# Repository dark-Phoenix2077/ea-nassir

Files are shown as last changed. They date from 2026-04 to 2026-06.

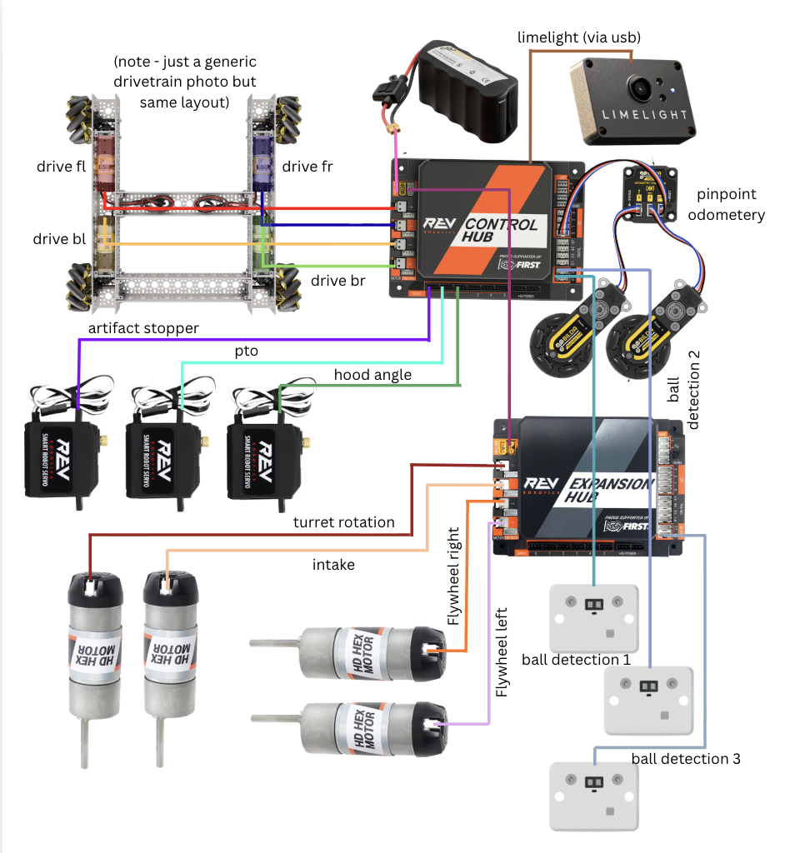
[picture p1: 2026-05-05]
wiring.png

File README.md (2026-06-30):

## ea-nassir 
A robot made to compete in the FTC decode season, built just to practise cad and coding skills =)

Screenshot 2026-04-23 at 11 40 23 am

## build photos





## why I made this

I wanted to attempt making a full FTC robot from scrach, on my own. despite my final design turning out very similar to widespread designs, I am happy just for building one of my own from scratch. I probably will not take part in any competitions, but I have been wanting to go through the whole process of building an FTC robot from start to finish, and the stasis hackathon finally gave me an excuse to do so.

## what there is

Currently, I have done the following:

CAD: The most complete, comprehensive part of the design, this consists of silicon molds for custom intake rollers, a drivetrain, 360 turret and PTO mechanism, all connected with custom CNC plates.

Screenshot 2026-04-23 at 12 18 12 pm

Screenshot 2026-04-23 at 12 18 51 pm

Screenshot 2026-04-23 at 12 19 32 pm

Screenshot 2026-04-23 at 12 31 41 pm

Coding: all set up and completed except for specific pedropathing parameters, will do when I build the physical robot (needs specific calibration)

Screenshot 2026-04-23 at 12 33 21 pm

(note that code is in /TeamCode/src/main/java/org/firstinspires/ftc/teamcode)

BOM: created a (as comprehensive as I could remember) BOM

Wiring: also added the wiring diagram for all motors/servos/sensors/etc. - in WIRING.md

## BOM

(note that this may not be final. also, most of these parts already exist with me)

Electronics & Control

| # | Name | Item Code | Qty | Notes | Link |
|---|---|---|-----|---|---|
| 1 | REV Control Hub | REV-31-1595 | 1 | Main robot controller | [Link](https://www.revrobotics.com/rev-31-1595/) |
| 2 | REV Expansion Hub | REV-31-1153 | 1 | Adds extra I/O ports | [Link](https://www.revrobotics.com/rev-31-1153/) |
| 3 | Axon MAX Servo | — | 2 | High-torque smart servo | [Link](https://axon-robotics.com/products/max) |
| 4 | GoBilda 5000 Series 12VDC Motor | 5000-0002-0001 | 2 | 12V DC motor, no encoder | [Link](https://www.gobilda.com/5000-series-12vdc-motor/) |
| 5 | GoBilda 5000 Series 12VDC Motor (REX Pinion Shaft) | 5000-0002-4008 | 1 | 12V DC motor with 8mm REX pinion shaft | [Link](https://www.gobilda.com/5000-series-12vdc-motor-with-8mm-rex-pinion-shaft/) |
| 6 | 5203 Series Yellow Jacket Planetary Gear Motor (13.7:1) | 5203-2402-0014 | 4 | 435 RPM, 8mm REX shaft, 3.3–5V encoder | [Link](https://www.gobilda.com/5203-series-yellow-jacket-planetary-gear-motor-13-7-1-ratio-24mm-length-8mm-rex-shaft-435-rpm-3-3-5v-encoder/) |
| 7 | 5203 Series Yellow Jacket Planetary Gear Motor (1:1) | 5203-242-0001 | 1 | 6000 RPM, 8mm REX shaft, 3.3–5V encoder | [Link](https://www.gobilda.com/5203-series-yellow-jacket-motor-1-1-ratio-24mm-length-8mm-rex-shaft-6000-rpm-3-3-5v-encoder/) |
| 8 | REV Through Bore Encoder | REV-11-3174 | 1 | Magnetic rotary encoder | [Link](https://www.revrobotics.com/rev-11-3174) |
| 9 | 6V Servo Power Injector (6 Channel, 8–15V Input) | 3125-0001-0001 | 1 | Powers servos independently from hubs | [Link](https://www.gobilda.com/6v-servo-power-injector-6-channel-8-15v-input/) |

 Sensors

| # | Name | Item Code | Qty | Notes | Link |
|---|---|---|-----|---|---|
| 10 | Swyft Ranger Distance Sensor | — | 3 | Distance sensor | [Link](https://swyftrobotics.com/products/swyft-ranger-distance-sensor) |
| 11 | REV Magnetic Limit Switch Bundle | REV-31-1462 | 1 | Bundle includes REV-40-1467 switch | [Link](https://www.revrobotics.com/rev-31-1462/) |
| 12 | REV Magnet Limit Switch (individual) | REV-40-1467 (inside REV-31-1462) | 1 | Part of the bundle above | [Link](https://www.revrobotics.com/rev-31-1462/) |

Odometry & Navigation

| # | Name | Item Code | Qty | Notes | Link |
|---|---|---|-----|---|---|
| 13 | GoBilda Pinpoint Odometry Pod (32mm wheel) | 3110-0001-0002 | 3 | 2 for drivetrain, 1 for other use | [Link](https://www.gobilda.com/4-bar-odometry-pod-32mm-wheel/) |

Drivetrain

| # | Name | Item Code | Qty | Notes | Link |
|---|---|---|-----|---|---|
| 14 | Mecanum Wheel Set 96mm (70A, Bearing Supported) | 3213-3606-0002 | 4 (1 pack of 4) | Main drivetrain wheels | [Link](https://www.gobilda.com/96mm-mecanum-wheel-set-70a-durometer-bearing-supported-rollers/) |
| 15 | 3417 Series 5mm HTD Pinion Timing Belt Pulley (8mm REX, 16T) | 3417-4008-0016 | 4 | Drivetrain belt drive | [Link](https://www.gobilda.com/3417-series-5mm-htd-pitch-set-screw-pinion-timing-belt-pulley-8mm-rex-bore-16-tooth/) |
| 16 | 5203 Yellow Jacket Motor — see Electronics | — | 4 | Listed under Electronics (#6) | — |

Turret

| # | Name | Item Code | Qty | Notes | Link |
|---|---|---|-----|---|---|
| 16 | KA070CPO Thin Section Bearing | KA070CPO | 1 | 177.8×190.5×6.35mm | [Link](https://zhongzhengbearing.en.made-in-china.com/product/PxOUjEkKZXhu/China-Thin-Section-Bearing-Ka070cpo-High-Quality-Bearing-Ka070cpo-Bearing-Size-177-8-190-5-6-35.h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) |
| 17 | 2mm Pitch GT2 Pinion Timing Pulley (8mm REX, 20T) | 3422-4008-0020 | 3 | 2 for turret, 1 for other use | [Link](https://www.gobilda.com/2mm-pitch-gt2-pinion-timing-pulley-8mm-rex-bore-20-tooth/) |
| 18 | 2mm Pitch GT2 Hub Mount Timing Belt Pulley (14mm Bore, 60T) | 3421-0014-0060 | 1 | Large driven pulley | [Link](https://www.gobilda.com/2mm-pitch-gt2-hub-mount-timing-belt-pulley-14mm-bore-60-tooth/) |
| 19 | GT2 Timing Belts for Turret | — | 2 | 2mm pitch GT2 belts | [Link](https://ar.aliexpress.com/i/32860465902.html) |
| 20 | 2302 Series Aluminum Mod 0.8 Hub Mount Gear (14mm Bore, 60T) | 2302-0014-0060 | 2 | Turret gear drive | [Link](https://www.gobilda.com/2302-series-aluminum-mod-0-8-hub-mount-gear-14mm-bore-60-tooth/) |
| 21 | 2303 Series Steel Mod 0.8 Pinion Gear (8mm REX, 20T) | 2303-4008-0020 | 1 | Pinion for turret gear drive | [Link](https://www.gobilda.com/2303-series-steel-mod-0-8-pinion-gear-8mm-rex-bore-20-tooth/) |

Wheels & Rollers

| # | Name | Item Code | Qty | Notes | Link |
|---|---|---|-----|---|---|
| 22 | 3614 Series Rhino Wheel (14mm Bore, 96mm, 30A) | 3614-0014-0096 | 1 | Soft rubber wheel | [Link](https://www.gobilda.com/3614-series-rhino-wheel-14mm-bore-96mm-diameter-30a-durometer/) |
| 23 | 3613 Series Gecko Wheel (14mm Bore, 96mm) | 3613-0014-0096 | 1 | High-grip gecko wheel | [Link](https://www.gobilda.com/3613-series-gecko-wheel-14mm-bore-96mm-diameter/) |
| 24 | 3613 Series Gecko Wheel (14mm Bore, 72mm) | 3613-0014-0072 | 2 | Smaller gecko wheel variant | [Link](https://www.gobilda.com/3613-series-gecko-wheel-14mm-bore-72mm-diameter/) |

Bearings

| # | Name | Item Code | Qty | Notes | Link |
|---|---|---|-----|---|---|
| 25 | 1611 Series Flanged Ball Bearing (8mm REX ID × 14mm OD, 5mm) | 1611-0514-4008 | 15 | 4 for turret, 11 for drivetrain | [Link](https://www.gobilda.com/1611-series-flanged-ball-bearing-8mm-rex-id-x-14mm-od-5mm-thickness-2-pack/) |
| 26 | Miniature Flange Bearings Assortment (MF52ZZ–MF148ZZ) | — | 10 | Various small flanged bearings | [Link](https://www.temu.com/ae/10pcs-mf52zz-mf62zz-mf63zz-mf74zz-mf83zz-mf84zz-to-mf148zz-miniature-flange-bearing-thin-wall-metal-shielded-flanged-bearings-g-6011014310470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) |

Hubs & Shafts

| # | Name | Item Code | Qty | Notes | Link |
|---|---|---|-----|---|---|
| 27 | 1310 Series Hyper Hub (8mm REX Bore) | 1310-0016-4008 | 5 | 1 for turret, 4 for drivetrain | [Link](https://www.gobilda.com/1310-series-hyper-hub-8mm-rex-bore/) |
| 28 | 1309 Series Sonic Hub (8mm REX Bore) | 1309-0016-4008 | 8 | 1 for turret, 7 for drivetrain | [Link](https://www.gobilda.com/1309-series-sonic-hub-8mm-rex-bore/) |
| 29 | 1906 Series Lightweight Servo Hub (25T Spline, 32mm) | 1906-0025-0032 | 3 | 2 for turret/arm, 1 for drivetrain | [Link](https://www.gobilda.com/1906-series-lightweight-servo-hub-25-tooth-spline-32mm-diameter/) |
| 30 | 8mm REX Shaft with E-Clip (Stainless, 192mm) | 2106-4008-1920 | 1 | Main shaft for turret/arm assembly | [Link](https://www.gobilda.com/8mm-rex-shaft-with-e-clip-stainless-steel-192mm-length/) |

Structural Components

| # | Name | Item Code | Qty | Notes | Link |
|---|---|---|-----|---|---|
| 31 | 1119 Series Shaft Beam (7-Hole, 56mm) | 1119-0007-0056 | 16 | 2 for turret, 14 for drivetrain | [Link](https://www.gobilda.com/1119-series-shaft-beam-7-hole-56mm-length/) |
| 32 | 1121 Series Low-Side U-Channel (9-Hole, 240mm) | 1121-0009-0240 | 2 | Drivetrain frame channel | [Link](https://www.gobilda.com/1121-series-low-side-u-channel-9-hole-240mm-length/) |
| 33 | 1205 Series Dual Block Mount (1.5) | 1205-0001-0005 | 10 | 4 for turret, 2 from turret pack, 4 for drivetrain | [Link](https://www.gobilda.com/1205-series-dual-block-mount-1-5-2-pack/) |

Standoffs

| # | Name | Item Code | Qty | Notes | Link |
|---|---|---|-----|---|---|
| 34 | 1516 Series 8mm REX Standoff (192mm) | 1516-4008-1920 | 5 | 4 for turret, 1 for drivetrain | [Link](https://www.gobilda.com/1516-series-8mm-rex-standoff-m4-x-0-7mm-threads-192mm-length-4-pack/) |
| 35 | 1516 Series 8mm REX Standoff (288mm) | 1516-4008-2880 | 3 | Drivetrain frame | [Link](https://www.gobilda.com/1516-series-8mm-rex-standoff-m4-x-0-7mm-threads-288mm-length-4-pack/) |
| 36 | 1501 Series M4 × 0.7mm Standoff (26mm) | 1501-0006-0260 | 16 | Drivetrain spacers | [Link](https://www.gobilda.com/1501-series-m4-x-0-7mm-standoff-6mm-od-26mm-length-4-pack/) |
| 37 | 1501 Series M4 × 0.7mm Standoff (16mm) | 1501-0006-0160 | 12 | Drivetrain spacers | [Link](https://www.gobilda.com/1501-series-m4-x-0-7mm-standoff-6mm-od-16mm-length-4-pack/) |
| 38 | 1501 Series M4 × 0.7mm Standoff (46mm) | 1501-0006-0460 | 12 | Drivetrain spacers | [Link](https://www.gobilda.com/1501-series-m4-x-0-7mm-standoff-6mm-od-46mm-length-4-pack/) |

Fasteners

| # | Name | Item Code | Qty | Notes | Link |
|---|---|---|-----|---|---|
| 39 | Zinc-Plated Steel Socket Head Screw M3 × 0.5mm × 12mm | 2800-0003-0012 | 8 | 6-pack | [Link](https://www.gobilda.com/zinc-plated-steel-socket-head-screw-m3-x-0-5mm-12mm-length-6-pack/) |
| 40 | Hex Socket Head Cap Screw M3 × 0.5mm × 5mm | — | 16 | Generic M3×5 cap screws | — |
| 41 | Zinc-Plated Steel Button Head Screw M4 × 0.7mm × 60mm (25-Pack) | 2802-0004-0060 | 1 pack | Long M4 bolts | [Link](https://www.gobilda.com/2802-series-zinc-plated-steel-button-head-screw-m4-x-0-7mm-60mm-length-25-pack/) |

Consumables & Misc

| # | Name | Item Code | Qty | Notes | Link |
|---|---|---|-----|---|---|
| 41 | Loctite Threadlocker Blue 242 (6mL) | 2922-0001-0001 | 2 | Thread locking compound | [Link](https://www.gobilda.com/loctite-threadlocker-blue-242-6ml/) |

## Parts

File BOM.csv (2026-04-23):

# | Name | Item Code | Qty | Notes | Link
1 | REV Control Hub | REV-31-1595 | 1 | Main robot controller | https://www.revrobotics.com/rev-31-1595/
2 | REV Expansion Hub | REV-31-1153 | 1 | Adds extra I/O ports | https://www.revrobotics.com/rev-31-1153/
3 | Axon MAX Servo | — | 2 | High-torque smart servo | https://axon-robotics.com/products/max
4 | GoBilda 5000 Series 12VDC Motor | 5000-0002-0001 | 2 | 12V DC motor no encoder | https://www.gobilda.com/5000-series-12vdc-motor/
5 | GoBilda 5000 Series 12VDC Motor (REX Pinion Shaft) | 5000-0002-4008 | 1 | 12V DC motor with 8mm REX pinion shaft | https://www.gobilda.com/5000-series-12vdc-motor-with-8mm-rex-pinion-shaft/
6 | 5203 Series Yellow Jacket Planetary Gear Motor (13.7:1) | 5203-2402-0014 | 4 | 435 RPM 8mm REX shaft 3.3–5V encoder | https://www.gobilda.com/5203-series-yellow-jacket-planetary-gear-motor-13-7-1-ratio-24mm-length-8mm-rex-shaft-435-rpm-3-3-5v-encoder/
7 | 5203 Series Yellow Jacket Planetary Gear Motor (1:1) | 5203-242-0001 | 1 | 6000 RPM 8mm REX shaft 3.3–5V encoder | https://www.gobilda.com/5203-series-yellow-jacket-motor-1-1-ratio-24mm-length-8mm-rex-shaft-6000-rpm-3-3-5v-encoder/
8 | REV Through Bore Encoder | REV-11-3174 | 1 | Magnetic rotary encoder | https://www.revrobotics.com/rev-11-3174
9 | 6V Servo Power Injector (6 Channel 8–15V Input) | 3125-0001-0001 | 1 | Powers servos independently from hubs | https://www.gobilda.com/6v-servo-power-injector-6-channel-8-15v-input/
10 | Swyft Ranger Distance Sensor | — | 3 | Distance sensor | https://swyftrobotics.com/products/swyft-ranger-distance-sensor
11 | REV Magnetic Limit Switch Bundle | REV-31-1462 | 1 | Bundle includes REV-40-1467 switch | https://www.revrobotics.com/rev-31-1462/
12 | REV Magnet Limit Switch (individual) | REV-40-1467 | 1 | Part of the bundle above | https://www.revrobotics.com/rev-31-1462/
13 | GoBilda Pinpoint Odometry Pod (32mm wheel) | 3110-0001-0002 | 3 | 2 for drivetrain 1 for other use | https://www.gobilda.com/4-bar-odometry-pod-32mm-wheel/
14 | Mecanum Wheel Set 96mm (70A Bearing Supported) | 3213-3606-0002 | 1 | Main drivetrain wheels (Pack of 4) | https://www.gobilda.com/96mm-mecanum-wheel-set-70a-durometer-bearing-supported-rollers/
15 | 3417 Series 5mm HTD Pinion Timing Belt Pulley (8mm REX 16T) | 3417-4008-0016 | 4 | Drivetrain belt drive | https://www.gobilda.com/3417-series-5mm-htd-pitch-set-screw-pinion-timing-belt-pulley-8mm-rex-bore-16-tooth/
16 | KA070CPO Thin Section Bearing | KA070CPO | 1 | 177.8x190.5x6.35mm | https://zhongzhengbearing.en.made-in-china.com/product/PxOUjEkKZXhu/China-Thin-Section-Bearing-Ka070cpo-High-Quality-Bearing-Ka070cpo-Bearing-Size-177-8-190-5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
17 | 2mm Pitch GT2 Pinion Timing Pulley (8mm REX 20T) | 3422-4008-0020 | 3 | 2 for turret 1 for other use | https://www.gobilda.com/2mm-pitch-gt2-pinion-timing-pulley-8mm-rex-bore-20-tooth/
18 | 2mm Pitch GT2 Hub Mount Timing Belt Pulley (14mm Bore 60T) | 3421-0014-0060 | 1 | Large driven pulley | https://www.gobilda.com/2mm-pitch-gt2-hub-mount-timing-belt-pulley-14mm-bore-60-tooth/
19 | GT2 Timing Belts for Turret | — | 2 | 2mm pitch GT2 belts | https://ar.aliexpress.com/i/32860465902.html
20 | 2302 Series Aluminum Mod 0.8 Hub Mount Gear (14mm Bore 60T) | 2302-0014-0060 | 2 | Turret gear drive | https://www.gobilda.com/2302-series-aluminum-mod-0-8-hub-mount-gear-14mm-bore-60-tooth/
21 | 2303 Series Steel Mod 0.8 Pinion Gear (8mm REX 20T) | 2303-4008-0020 | 1 | Pinion for turret gear drive | https://www.gobilda.com/2303-series-steel-mod-0-8-pinion-gear-8mm-rex-bore-20-tooth/
22 | 3614 Series Rhino Wheel (14mm Bore 96mm 30A) | 3614-0014-0096 | 1 | Soft rubber wheel | https://www.gobilda.com/3614-series-rhino-wheel-14mm-bore-96mm-diameter-30a-durometer/
23 | 3613 Series Gecko Wheel (14mm Bore 96mm) | 3613-0014-0096 | 1 | High-grip gecko wheel | https://www.gobilda.com/3613-series-gecko-wheel-14mm-bore-96mm-diameter/
24 | 3613 Series Gecko Wheel (14mm Bore 72mm) | 3613-0014-0072 | 2 | Smaller gecko wheel variant | https://www.gobilda.com/3613-series-gecko-wheel-14mm-bore-72mm-diameter/
25 | 1611 Series Flanged Ball Bearing (8mm REX ID x 14mm OD 5mm) | 1611-0514-4008 | 15 | 4 for turret 11 for drivetrain | https://www.gobilda.com/1611-series-flanged-ball-bearing-8mm-rex-id-x-14mm-od-5mm-thickness-2-pack/
26 | Miniature Flange Bearings Assortment (MF52ZZ–MF148ZZ) | — | 10 | Various small flanged bearings | https://www.temu.com/ae/10pcs-mf52zz-mf62zz-mf63zz-mf74zz-mf83zz-mf84zz-to-mf148zz-miniature-flange-bearing-thin-wall-metal-shielded-flanged-bearings-g-601101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
27 | 1310 Series Hyper Hub (8mm REX Bore) | 1310-0016-4008 | 5 | 1 for turret 4 for drivetrain | https://www.gobilda.com/1310-series-hyper-hub-8mm-rex-bore/
28 | 1309 Series Sonic Hub (8mm REX Bore) | 1309-0016-4008 | 8 | 1 for turret 7 for drivetrain | https://www.gobilda.com/1309-series-sonic-hub-8mm-rex-bore/
29 | 1906 Series Lightweight Servo Hub (25T Spline 32mm) | 1906-0025-0032 | 3 | 2 for turret/arm 1 for drivetrain | https://www.gobilda.com/1906-series-lightweight-servo-hub-25-tooth-spline-32mm-diameter/
30 | 8mm REX Shaft with E-Clip (Stainless 192mm) | 2106-4008-1920 | 1 | Main shaft for turret/arm assembly | https://www.gobilda.com/8mm-rex-shaft-with-e-clip-stainless-steel-192mm-length/
31 | 1119 Series Shaft Beam (7-Hole 56mm) | 1119-0007-0056 | 16 | 2 for turret 14 for drivetrain | https://www.gobilda.com/1119-series-shaft-beam-7-hole-56mm-length/
32 | 1121 Series Low-Side U-Channel (9-Hole 240mm) | 1121-0009-0240 | 2 | Drivetrain frame channel | https://www.gobilda.com/1121-series-low-side-u-channel-9-hole-240mm-length/
33 | 1205 Series Dual Block Mount (1.5) | 1205-0001-0005 | 10 | 4 for turret 2 from turret pack 4 for drivetrain | https://www.gobilda.com/1205-series-dual-block-mount-1-5-2-pack/
34 | 1516 Series 8mm REX Standoff (192mm) | 1516-4008-1920 | 5 | 4 for turret 1 for drivetrain | https://www.gobilda.com/1516-series-8mm-rex-standoff-m4-x-0-7mm-threads-192mm-length-4-pack/
35 | 1516 Series 8mm REX Standoff (288mm) | 1516-4008-2880 | 3 | Drivetrain frame | https://www.gobilda.com/1516-series-8mm-rex-standoff-m4-x-0-7mm-threads-288mm-length-4-pack/
36 | 1501 Series M4 x 0.7mm Standoff (26mm) | 1501-0006-0260 | 16 | Drivetrain spacers | https://www.gobilda.com/1501-series-m4-x-0-7mm-standoff-6mm-od-26mm-length-4-pack/
37 | 1501 Series M4 x 0.7mm Standoff (16mm) | 1501-0006-0160 | 12 | Drivetrain spacers | https://www.gobilda.com/1501-series-m4-x-0-7mm-standoff-6mm-od-16mm-length-4-pack/
38 | 1501 Series M4 x 0.7mm Standoff (46mm) | 1501-0006-0460 | 12 | Drivetrain spacers | https://www.gobilda.com/1501-series-m4-x-0-7mm-standoff-6mm-od-46mm-length-4-pack/
39 | Zinc-Plated Steel Socket Head Screw M3 x 0.5mm x 12mm | 2800-0003-0012 | 8 | 6-pack | https://www.gobilda.com/zinc-plated-steel-socket-head-screw-m3-x-0-5mm-12mm-length-6-pack/
40 | Hex Socket Head Cap Screw M3 x 0.5mm x 5mm | — | 16 | Generic M3x5 cap screws
41 | Zinc-Plated Steel Button Head Screw M4 x 0.7mm x 60mm | 2802-0004-0060 | 1 | 25-pack | https://www.gobilda.com/2802-series-zinc-plated-steel-button-head-screw-m4-x-0-7mm-60mm-length-25-pack/
42 | Loctite Threadlocker Blue 242 (6mL) | 2922-0001-0001 | 2 | Thread locking compound | https://www.gobilda.com/loctite-threadlocker-blue-242-6ml/

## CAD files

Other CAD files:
CAD/EA-NASSIR.step

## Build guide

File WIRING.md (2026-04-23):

(fyi, no solder is needed, it is all plug-and play, with a bit of coding magic of course)

Control Hub

Motor ports:

Port 0 - fl - Front Left drive, GoBilda 5203 312RPM, REVERSED

Port 1 - fr - Front Right drive, GoBilda 5203 312RPM, FORWARD

Port 2 - bl - Back Left drive, GoBilda 5203 312RPM, REVERSED

Port 3 - br - Back Right drive, GoBilda 5203 312RPM, FORWARD

Servo ports:

Port 0 - stopper - ball stopper, REV Smart Servo

Port 1 - pto - PTO actuator, REV Smart Servo, inverted

Port 2 - hood - Flywheel hood angle, REV Smart Servo

I2C ports:

Port 1 - pinpoint — GoBilda Pinpoint Odometry Computer, address 0x31
USB:

Port 0 AprilTag camera (used by AprilTagTracking)
Expansion Hub

Motor ports:

Port 0 - turret - Turret rotation, GoBilda 5203 60RPM, inverted via setInverted(true)

Port 1 - intake - Intake/PTO motor, GoBilda 5203 312RPM, REVERSED

Port 2 - rsh - Right flywheel, GoBilda 5203 (high RPM variant), FORWARD

Port 3 - lsm - Left flywheel, GoBilda 5203 (high RPM variant), FORWARD

Analog input ports:

Port 0 - s1 - Intake ball sensor 1, SWYFT analog distance sensor

Port 1 - s2 - Intake ball sensor 2, SWYFT analog distance sensor

Port 2 - s3 - Intake ball sensor 3, SWYFT analog distance sensor

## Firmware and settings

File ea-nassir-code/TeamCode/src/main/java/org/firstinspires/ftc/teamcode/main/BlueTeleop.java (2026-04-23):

package org.firstinspires.ftc.teamcode.main;

import static org.firstinspires.ftc.teamcode.globals.Localization.getBlueDistance;
import static org.firstinspires.ftc.teamcode.globals.Localization.getHeading;
import static org.firstinspires.ftc.teamcode.globals.Localization.getPose;
import static org.firstinspires.ftc.teamcode.globals.Localization.getRedDistance;
import static org.firstinspires.ftc.teamcode.globals.RobotConstants.blueGoalPose;
import static org.firstinspires.ftc.teamcode.globals.RobotConstants.chosenAlliance;
import static org.firstinspires.ftc.teamcode.globals.RobotConstants.farRedGoalPose;
import static org.firstinspires.ftc.teamcode.globals.RobotConstants.intakeBlueRamp;
import static org.firstinspires.ftc.teamcode.globals.RobotConstants.intakeRedRamp;
import static org.firstinspires.ftc.teamcode.globals.RobotConstants.redGoalPose;
import static org.firstinspires.ftc.teamcode.globals.RobotConstants.redPark;
import static org.firstinspires.ftc.teamcode.globals.RobotConstants.redRampCP;
import static org.firstinspires.ftc.teamcode.globals.RobotConstants.resetPos;
import static org.firstinspires.ftc.teamcode.globals.RobotConstants.savedPose;
import static org.firstinspires.ftc.teamcode.pedroPathing.Constants.createFollower;
import static org.firstinspires.ftc.teamcode.pedroPathing.Tuning.follower;

import com.bylazar.telemetry.PanelsTelemetry;
import com.bylazar.telemetry.TelemetryManager;
import com.pedropathing.follower.Follower;
import com.pedropathing.geometry.BezierCurve;
import com.pedropathing.geometry.BezierLine;
import com.pedropathing.geometry.Pose;
import com.pedropathing.paths.HeadingInterpolator;
import com.pedropathing.paths.PathPoint;
import com.qualcomm.hardware.lynx.LynxModule;
import com.qualcomm.robotcore.eventloop.opmode.OpMode;
import com.qualcomm.robotcore.eventloop.opmode.TeleOp;
import com.qualcomm.robotcore.hardware.DcMotorEx;
import com.qualcomm.robotcore.hardware.DcMotorSimple;
import com.qualcomm.robotcore.util.ElapsedTime;
import com.skeletonarmy.marrow.zones.Point;
import com.skeletonarmy.marrow.zones.PolygonZone;

import org.firstinspires.ftc.teamcode.globals.Localization;
import org.firstinspires.ftc.teamcode.globals.RobotConstants;
import org.firstinspires.ftc.teamcode.subsystems.Intake;
import org.firstinspires.ftc.teamcode.subsystems.Shooter;
import org.firstinspires.ftc.teamcode.subsystems.Turret;
import org.firstinspires.ftc.teamcode.util.PIDFController;
import org.firstinspires.ftc.teamcode.vision.AprilTagTracking;

import java.util.List;

@TeleOp(name = "Blue Teleop Practice", group = "TeleOp")
public class BlueTeleop extends OpMode {
    private TelemetryManager telemetryM;
    private PIDFController controller1, controller2;
    private DcMotorEx sh;
    private DcMotorEx sh2;
    public static double targetVelocity, velocity1, velocity2;
    public static double P,I,kV,kS;

    private boolean newShooter = false;
    private Turret turret;
    public boolean activeHood = false;
    private Follower follower;
    private Shooter shooter;
    private Intake intake;

    private double yOffset = 0;
    private int speed = 0;
    private boolean autoAim = false;
    private double hoodPos = 0.7;
    private double sensitivity = 1;
    private ElapsedTime elapsedtime;
    private AprilTagTracking vision;
    private PolygonZone closeLaunchZone, farLaunchZone, robotZone;
    List<LynxModule> allHubs;
    private int loopCounter = 0;

    public void init() {
        elapsedtime = new ElapsedTime();
        elapsedtime.reset();
        chosenAlliance = "BLUE";
        Shooter.landAngle = Math.toRadians(-7);
        telemetryM = PanelsTelemetry.INSTANCE.getTelemetry();
        sh = hardwareMap.get(DcMotorEx.class, "rsh");
        closeLaunchZone = new PolygonZone(new Point(144, 144), new Point(72, 72), new Point(0, 144));
        farLaunchZone = new PolygonZone(new Point(48, 0), new Point(72, 24), new Point(96, 0));
        allHubs = hardwareMap.getAll(LynxModule.class);
        sh2 = hardwareMap.get(DcMotorEx.class, "lsm");
        shooter = new Shooter(hardwareMap, telemetryM);
        sh.setDirection(DcMotorSimple.Direction.FORWARD);
        sh2.setDirection(DcMotorSimple.Direction.FORWARD);
//        robotZone = new PolygonZone(17, 17);
        vision = new AprilTagTracking(hardwareMap);
        Shooter.shooterDistanceBiasInches = 0;
        turret = new Turret(hardwareMap, telemetryM);
        turret.setAutoAim(true);
//        turret.resetTurretEncoder();
        intake = new Intake(hardwareMap, telemetryM);
        intake.setStopper(0.48);
        follower = createFollower(hardwareMap);
        if (savedPose != null && Math.abs(savedPose.getHeading()) > 1) {
            follower.setStartingPose(savedPose);
        } else {
            follower.setStartingPose(new Pose(89, 78, Math.toRadians(0)).mirror());
        }
        Localization.init(follower, telemetryM);
        telemetryM.addLine("Initialized");
        telemetry.addData("saved Pose:", savedPose);
        blueGoalPose  = new Pose(2, 141, Math.toRadians(90));
        telemetry.update();
        telemetryM.update();
    }

    public void start() {
        follower.startTeleOpDrive(false);
        shooter.setHood(hoodPos);
        for (LynxModule module : allHubs) {
            module.setBulkCachingMode(LynxModule.BulkCachingMode.MANUAL);
        }
    }

    @Override
    public void loop() {
        for (LynxModule module : allHubs) {
            module.clearBulkCache();
        }

        double shotDistance = follower.getPose().distanceFrom(blueGoalPose);
        double actualShotSpeed = Math.abs(0.5 * (sh.getVelocity() - sh2.getVelocity()));
        double compensatedHoodPos = Shooter.getLowAngleHoodFromDistanceAndSpeed(shotDistance, actualShotSpeed);
        double[] coefficients = Shooter.getCoefficientsFromDistance(shotDistance);
        targetVelocity = coefficients[1] - 40;
        if (Math.abs(actualShotSpeed - targetVelocity) > 30) {
            hoodPos = Shooter.getLowAngleHoodFromDistanceAndSpeed(shotDistance, sh.getVelocity());
        } else {
            hoodPos = coefficients[0];
        }
        if (activeHood) {
            shooter.setHood(hoodPos);
        }

        if (Math.max(0, getBlueDistance() - 110)>0){
            targetVelocity += 110;
        }



        velocity1 = sh.getVelocity();
        velocity2 = sh2.getVelocity();


        if(intake.areAllBallsDetected()) {
            gamepad1.rumble(200);
            gamepad2.rumble(200);
        }

        if (gamepad1.right_trigger > 0.1) {
            sensitivity = 0.5;
        } else {
            sensitivity = 1;
        }

        if (gamepad1.dpadDownWasReleased()) {
            blueGoalPose  = new Pose(blueGoalPose.getX(), blueGoalPose.getY() - 1, Math.toRadians(90));
        }
        if (gamepad1.dpadUpWasReleased()) {
            blueGoalPose  = new Pose(blueGoalPose.getX(), blueGoalPose.getY() + 1, Math.toRadians(90));
        }
        if (gamepad1.dpadLeftWasReleased()) {
            blueGoalPose  = new Pose(blueGoalPose.getX() + 1, blueGoalPose.getY(), Math.toRadians(90));        }
        if (gamepad1.dpadRightWasReleased()) {
            blueGoalPose  = new Pose(blueGoalPose.getX() - 1, blueGoalPose.getY(), Math.toRadians(90));        }



        if (gamepad1.rightBumperWasPressed()) {
            if ((follower.getPose().distanceFrom(intakeRedRamp) < 20))
            {
                follower.followPath(follower.pathBuilder()
                        .addPath(new BezierCurve(
                                follower.getPose(),
                                redRampCP,
                                intakeRedRamp
                        ))
                        .setConstantHeadingInterpolation(intakeRedRamp.getHeading())
                        .build());
            }
            else {
                follower.followPath(follower.pathBuilder()
                        .addPath(new BezierCurve(
                                follower.getPose(),
                                redRampCP,
                                intakeRedRamp
                        ))
                        .setHeadingInterpolation(
                                HeadingInterpolator.piecewise(
                                        new HeadingInterpolator.PiecewiseNode(
                                                0,
                                                .5,
                                                HeadingInterpolator.constant(Math.toRadians(0))
                                        ),
                                        new HeadingInterpolator.PiecewiseNode(
                                                .5,
                                                1.0,
                                                HeadingInterpolator.constant(intakeRedRamp.getHeading()))
                                )
                        )
                        .build());
            }
        }
        else if (gamepad1.rightBumperWasReleased()) {
            follower.startTeleOpDrive(false);
        }

        if (gamepad1.leftBumperWasPressed()) {
            follower.followPath(follower.pathBuilder()
                    .addPath(new BezierLine(
                            follower.getPose(),
                            new Pose(84, 75)
                    ))
                    .setHeadingInterpolation(
                            HeadingInterpolator.piecewise(
                                    new HeadingInterpolator.PiecewiseNode(
                                            0,
                                            1.0,
                                            HeadingInterpolator.tangent.reverse()
                                    )
                            ))
                    .build());
        }
        else if (gamepad1.leftBumperWasReleased()) {
            follower.startTeleOpDrive(false);
        }



        follower.setTeleOpDrive(
                -gamepad1.left_stick_y * sensitivity,
                -gamepad1.left_stick_x * sensitivity,
                -gamepad1.right_stick_x * sensitivity
        );
        if (gamepad1.a) {
            hoodPos = compensatedHoodPos;
            shooter.setHood(hoodPos);
            intake.intake1On();
        }
        if (gamepad2.right_bumper) {
           intake.intake1On();
        }

        if (gamepad2.rightBumperWasReleased()) {
            intake.intakeOff();
        }

        if (gamepad2.left_bumper) {
            intake.engagePTO();
            intake.setStopper(0.35);
            activeHood = true;
            double farExtraInches = Math.max(0, getBlueDistance() - 110);
            if(farExtraInches > 0) {
                intake.onSpeed(1.0);
            }
            else {
                intake.onSpeed(1);
            }
        }
        else if (gamepad2.leftBumperWasReleased()) {
            intake.intakeOff();
            activeHood = false;
            intake.setStopper(0.48);
        }

        if (gamepad1.optionsWasPressed()) {
            follower.setPose(new Pose(135,9,Math.toRadians(90)));
        }


        if (sh.getVelocity() > targetVelocity) {
            sh.setPower(0);
            sh2.setPower(0);
        }
        else if (sh.getVelocity() < targetVelocity) {
            sh.setPower(1);
            sh2.setPower(1);
        }
        else {
            sh.setPower(0);
            sh2.setPower(0);
        }


        loopCounter +=1;

        Localization.update();
        turret.periodic();
        intake.periodic();

        telemetry.update();

    }
}

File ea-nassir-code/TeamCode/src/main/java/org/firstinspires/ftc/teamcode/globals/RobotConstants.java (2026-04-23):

package org.firstinspires.ftc.teamcode.globals;

import com.pedropathing.geometry.Pose;
import com.seattlesolvers.solverslib.hardware.SensorDistanceEx;
import com.seattlesolvers.solverslib.hardware.motors.MotorEx;
import com.seattlesolvers.solverslib.hardware.servos.ServoEx;

public class RobotConstants {
    public static double maxTurretPos = 523.5;
    public static double minTurretPos = -523.5;

    public MotorEx frontRight;
    public MotorEx frontLeft;
    public MotorEx backRight;
    public MotorEx backLeft;

    public ServoEx sIntakeA;
    public ServoEx sIntakeB;

    public SensorDistanceEx R1;
    public SensorDistanceEx R2;
    public SensorDistanceEx R3;

    public MotorEx intake;

    public MotorEx shooterA;
    public MotorEx shooterB;

    public static int maxEPT = 1900;

    // Calibrated hood map: 35deg -> 0.625, 65deg -> 1.0
    public static double maxHoodPos = 0.625;
    public static double minHoodPos = 1;
    public static double maxHoodAngle = 35;
    public static double minHoodAngle = 65;

    public static Pose blueGoalPose = new Pose(2, 141, Math.toRadians(90));
    public static Pose redGoalPose  = new Pose(141, 141, Math.toRadians(90));
    public static Pose farRedGoalPose = new Pose(140.4, 142);

    public static Pose redDistancePose = new Pose(138, 138, Math.toRadians(90));


    public static final int RED_GOAL_TAG_ID = 24;
    public static final int BLUE_GOAL_TAG_ID = 20;

    public static double engagePos = 0.1;
    public static double disengagePos = 0.5;

    public static final Pose resetPos = new Pose(135, 9, Math.toRadians(0));

    public static String chosenAlliance = "RED";
    public static Pose savedPose = null;

    public static Pose blueRampCP = new Pose(30.68223350253807, 58.12994923857866);
    public static Pose intakeRedRamp = new Pose(136, 57.7, Math.toRadians(26));
    public static Pose intakeRedRampDrifted = new Pose(135, 58.0, Math.toRadians(31));
    public static Pose intakeBlueRamp = intakeRedRamp.mirror();
    public static Pose redRampCP = new Pose(124, 60);
    public static Pose bluePark = new Pose(53.076142131979694, 23.350253807106576, Math.toRadians(180));
    public static Pose redPark = new Pose(53.076142131979694, 23.350253807106576, Math.toRadians(0));



}

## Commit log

2026-04-23 Fixed: Added ea-nassir-code files directly
    [app_settings.xml]
2026-04-23 Added robot CAD
    [EA-NASSIR.step]
2026-04-23 added BOM
2026-04-23 added WIRING.md
2026-04-23 Update README.md
    Updated project description and clarified wiring diagram location.
2026-04-23 added a CSV variant to the BOM, as per the docs
    [BOM.csv]
2026-04-23 fixed csv error
    [BOM.csv]
2026-04-23 maybe? fixed csv errrors
    [BOM.csv]
2026-05-05 added visual wiring diagram
2026-05-05 made self funding clear in bom
